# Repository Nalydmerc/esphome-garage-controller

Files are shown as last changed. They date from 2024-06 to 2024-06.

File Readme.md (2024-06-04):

### ESPHome Garage Door Controller

I am a forgetful man. I forget to close the garage door. My wife gets frustrated that I forget to close the garage door. I may or may not get slightly banned from the garage due to leaving the garage door open too many times after leaving for work. So, I do what any sensible man would do. I offload my responsibilities to technology, of course.

The device uses an ESP8266 running ESPHome to connect to HomeAssistant and do garage door things. I used a hall effect sensor to detect if each door was open or closed, but you could use any contact that opens/closes depending on the state of the door. To open and close the doors, I just wired in a relay in parallel with each button. YMMV, but for mine this did mean I had to physically disassemble each button and solder extra wires onto the PCB.

This project was designed to be cheap, as opposed to involved. You can build your own buck converters into your projects (I have in the past), but at the end of the day it's still cheaper to buy one of those cheap adjustable converters on aliexpress and call it a day. Sure there's 0.4V of switching noise, but the D1 Mini has a built in LDO anyway, as do most cheap development boards. ¯\\\_(ツ)\_/¯ A good project is one that is finished to spec, and my spec is that it works.

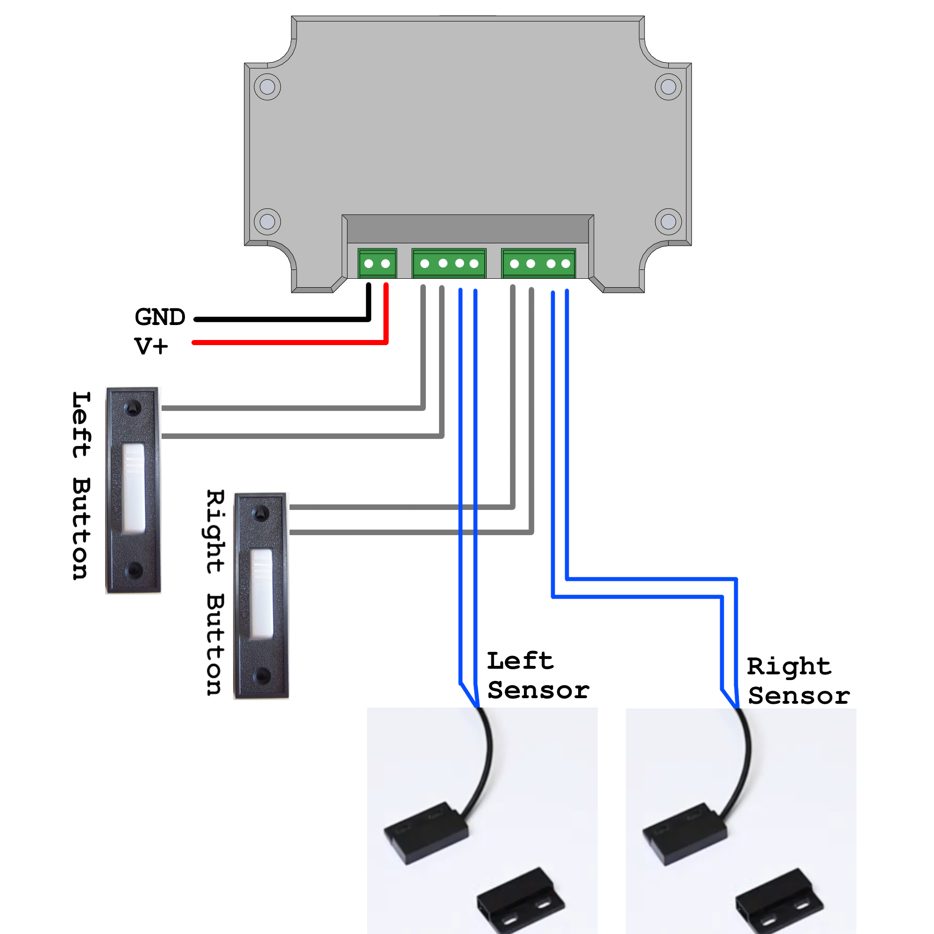
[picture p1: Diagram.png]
diagram


### Mechanical Assembly and Bill of Materials

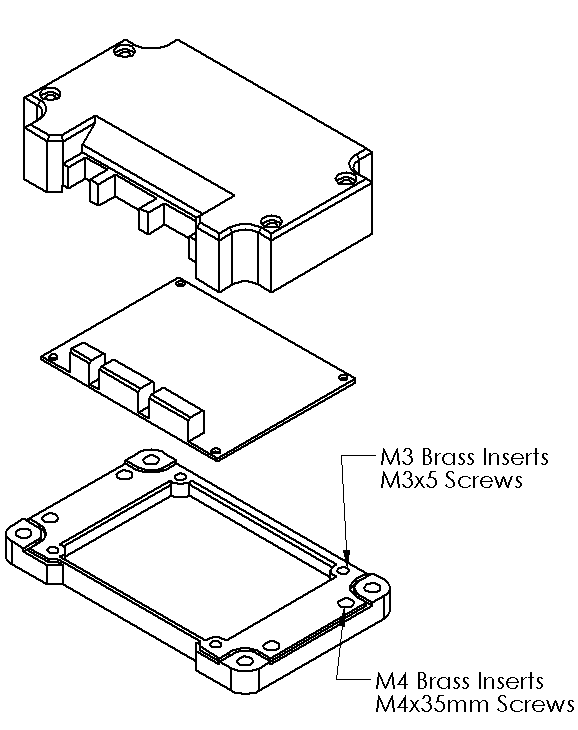
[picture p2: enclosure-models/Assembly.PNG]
mechanical assembly


.step files for a 3D printed enclosure are included in this project. The backplate uses M3 screws to mount the PCB, and M4 screws to attach the top. Other Non-PCB materials are as follows:

|Item | Qty|Link |
|--|--|--|
| Hall effect sensor |2| https://www.aliexpress.us/item/3256805925218267.html |
| Cabling || https://www.aliexpress.us/item/3256806428440404.html |
|Wire Ferrules (for crimping ends) || https://www.aliexpress.us/item/3256805075641713.html |
| Lever-nut connectors (love these) || https://www.aliexpress.us/item/3256803684080411.html |
| M3 Brass Inserts | 4 | https://www.aliexpress.us/item/3256803396040989.html |
| M3x5mm |4||
| M4 Brass Inserts | 4 | https://www.aliexpress.us/item/3256803396040989.html |
| M4x35mm |4||

### Manufacturing the PCB

If you want to make this PCB yourself, simply zip up the outputs folder and upload it to the PCB manufacturer of your choice. You can take the bill of materials CSV and upload it directly to digikey to create a cart with the needed components. Anything that doesn't have a digikey part number, I listed the relevant aliexpress product page.

### Random notes for myself

Reminder: Set switches to pins 5 and 4 to prevent them from toggling during startup. (esp8266s are weird. Never before have I had to deal with GPIOs just doing random things during the startup process.)

https://community.home-assistant.io/t/esp8266-relay-active-low-how-to-prevent-triggering-on-boot-or-reset-solved/88279/30
https://rabbithole.wwwdotorg.org/2017/03/28/esp8266-gpio.html

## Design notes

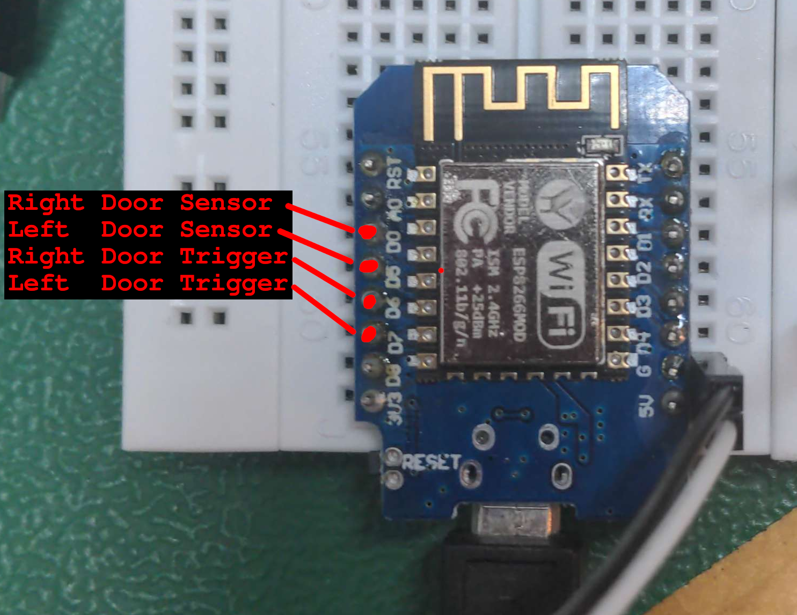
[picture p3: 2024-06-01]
prototype/Pinout.png

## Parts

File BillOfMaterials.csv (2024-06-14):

Reference | Value | Footprint | Qty | DNP | Digikey PN | PN
D1,D2 | 1N4148TR | Diode_THT:D_DO-35_SOD27_P10.16mm_Horizontal | 2 |  | 1N4148FSCT-ND | DIO-004
D3 | SMAJ12A | Diode_SMD:D_SMA_Handsoldering | 1 |  | SMAJ12ALFCT-ND | DIO-014
D4,D5 | SMA6J5.0A-TR | Diode_SMD:D_SMA_Handsoldering | 2 |  | 497-5938-1-ND | DIO-011
H1,H2,H3,H4 | MountingHole | MountingHole:MountingHole_3.2mm_M3 | 4
J1 | 1935161.0 | TerminalBlock:TerminalBlock_bornier-2_P5.08mm | 1 |  | https://www.aliexpress.us/item/3256805408760426.html | CON-005
J2,J3 | EB21A-04-C | TerminalBlock:TerminalBlock_bornier-4_P5.08mm | 2 |  | https://www.aliexpress.us/item/3256805408760426.html
JP1 | Jumper_2_Bridged | Connector_PinHeader_2.54mm:PinHeader_1x02_P2.54mm_Vertical | 1 |  | S9337-ND
K1,K2 | SRD-12VDC-SL-C | 000-Footprints:Relay_SPDT_Songle | 2 |  | https://www.aliexpress.us/item/3256802839040760.html
Q1,Q2 | BS170-D26Z | Package_TO_SOT_THT:TO-92_Inline_Wide | 2 |  | BS170-D26ZCT-ND | FET-002
Q3 | IRFR9024NTRLPBF | Package_TO_SOT_SMD:TO-252-2 | 1 |  | IRFR9024NTRLPBFCT-ND | FET-007
R1,R2,R3,R4 | 100k | Resistor_THT:R_Axial_DIN0207_L6.3mm_D2.5mm_P15.24mm_Horizontal | 4
S1 | EG1224 | 000-Footprints:SW_E-Switch_EG1224_SPDT_Angled | 1 |  | EG2585-ND | MISC-006
TP1,TP2,TP3,TP4,TP5 | TestPoint | TestPoint:TestPoint_Pad_1.5x1.5mm | 5
U1 | LM2596 | 000-Footprints:LM2596Module | 1 |  | https://www.aliexpress.us/item/3256804718557368.html | MISC-009
U2 | WeMos_D1_mini | 000-Footprints:wemos-d1-mini-with-pin-header-and-connector | 1 |  | https://www.aliexpress.us/item/3256805831695231.html

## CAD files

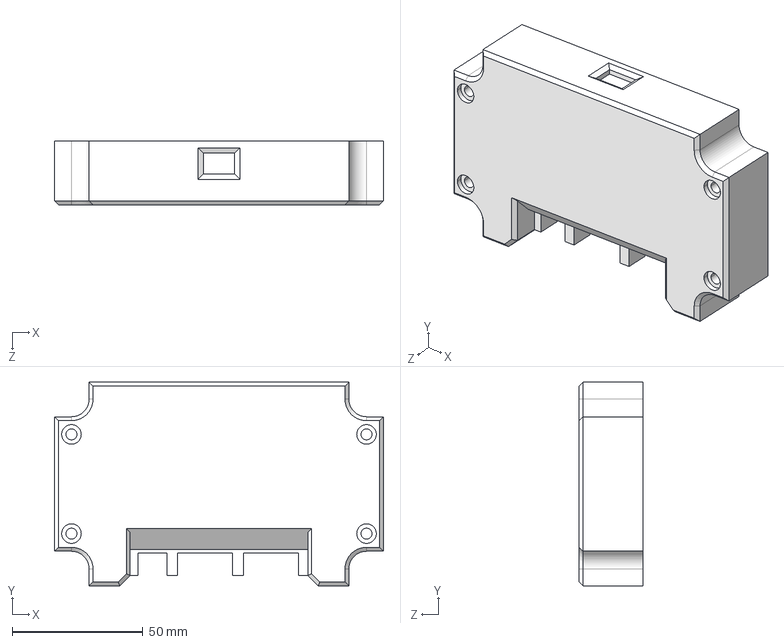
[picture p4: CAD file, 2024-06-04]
enclosure-models/Top.STEP
126.0 x 78.0 x 24.4 mm

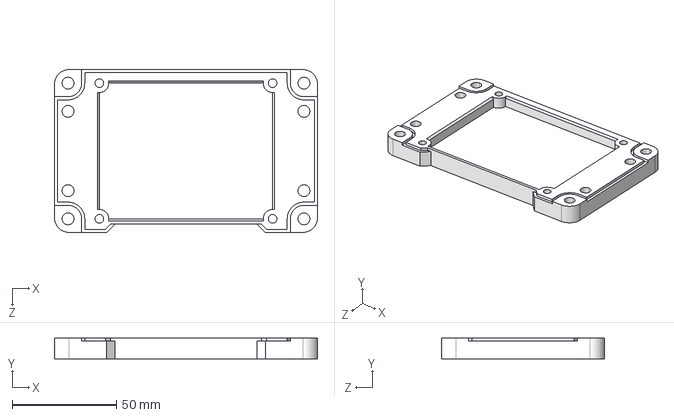
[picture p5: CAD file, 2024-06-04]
enclosure-models/Baseplate.STEP
126.0 x 10.0 x 78.0 mm

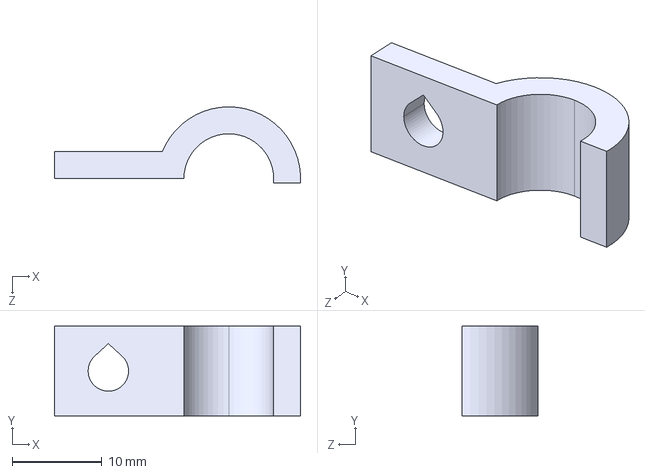
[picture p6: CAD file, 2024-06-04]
enclosure-models/Wireclip.STEP
27.4 x 10.0 x 8.50 mm

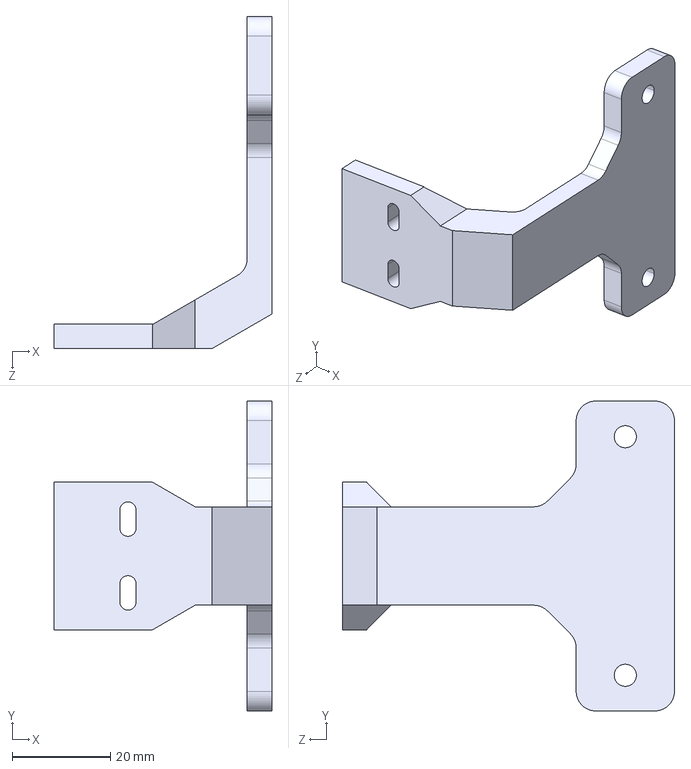
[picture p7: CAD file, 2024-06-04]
enclosure-models/SensorBracket.STEP
44.2 x 63.0 x 67.5 mm

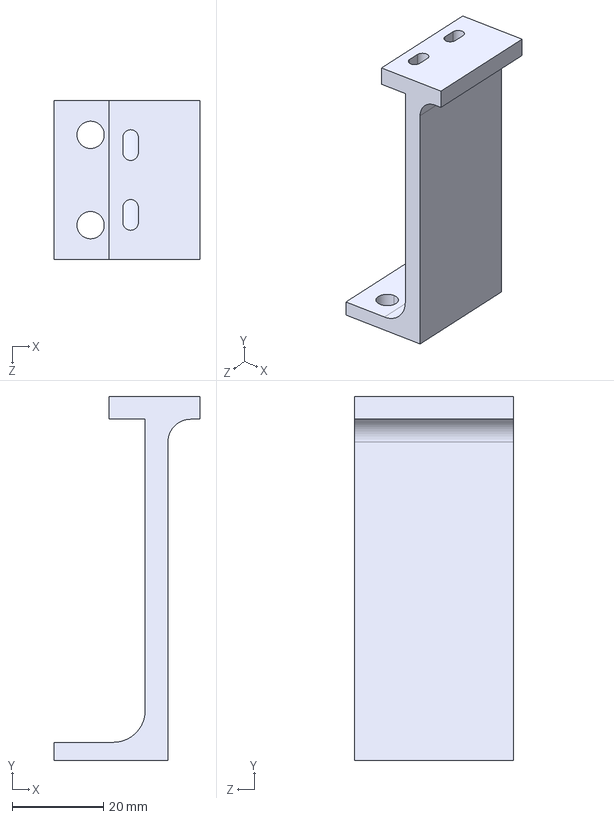
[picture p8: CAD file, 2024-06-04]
enclosure-models/MagnetBracket.STEP
32.0 x 80.0 x 35.0 mm

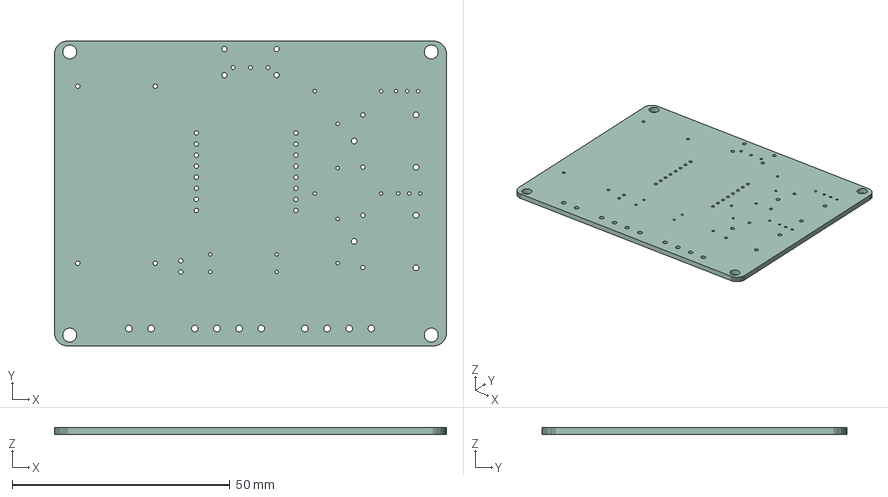
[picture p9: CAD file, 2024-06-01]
enclosure-models/pcb.step
90.0 x 70.0 x 1.60 mm

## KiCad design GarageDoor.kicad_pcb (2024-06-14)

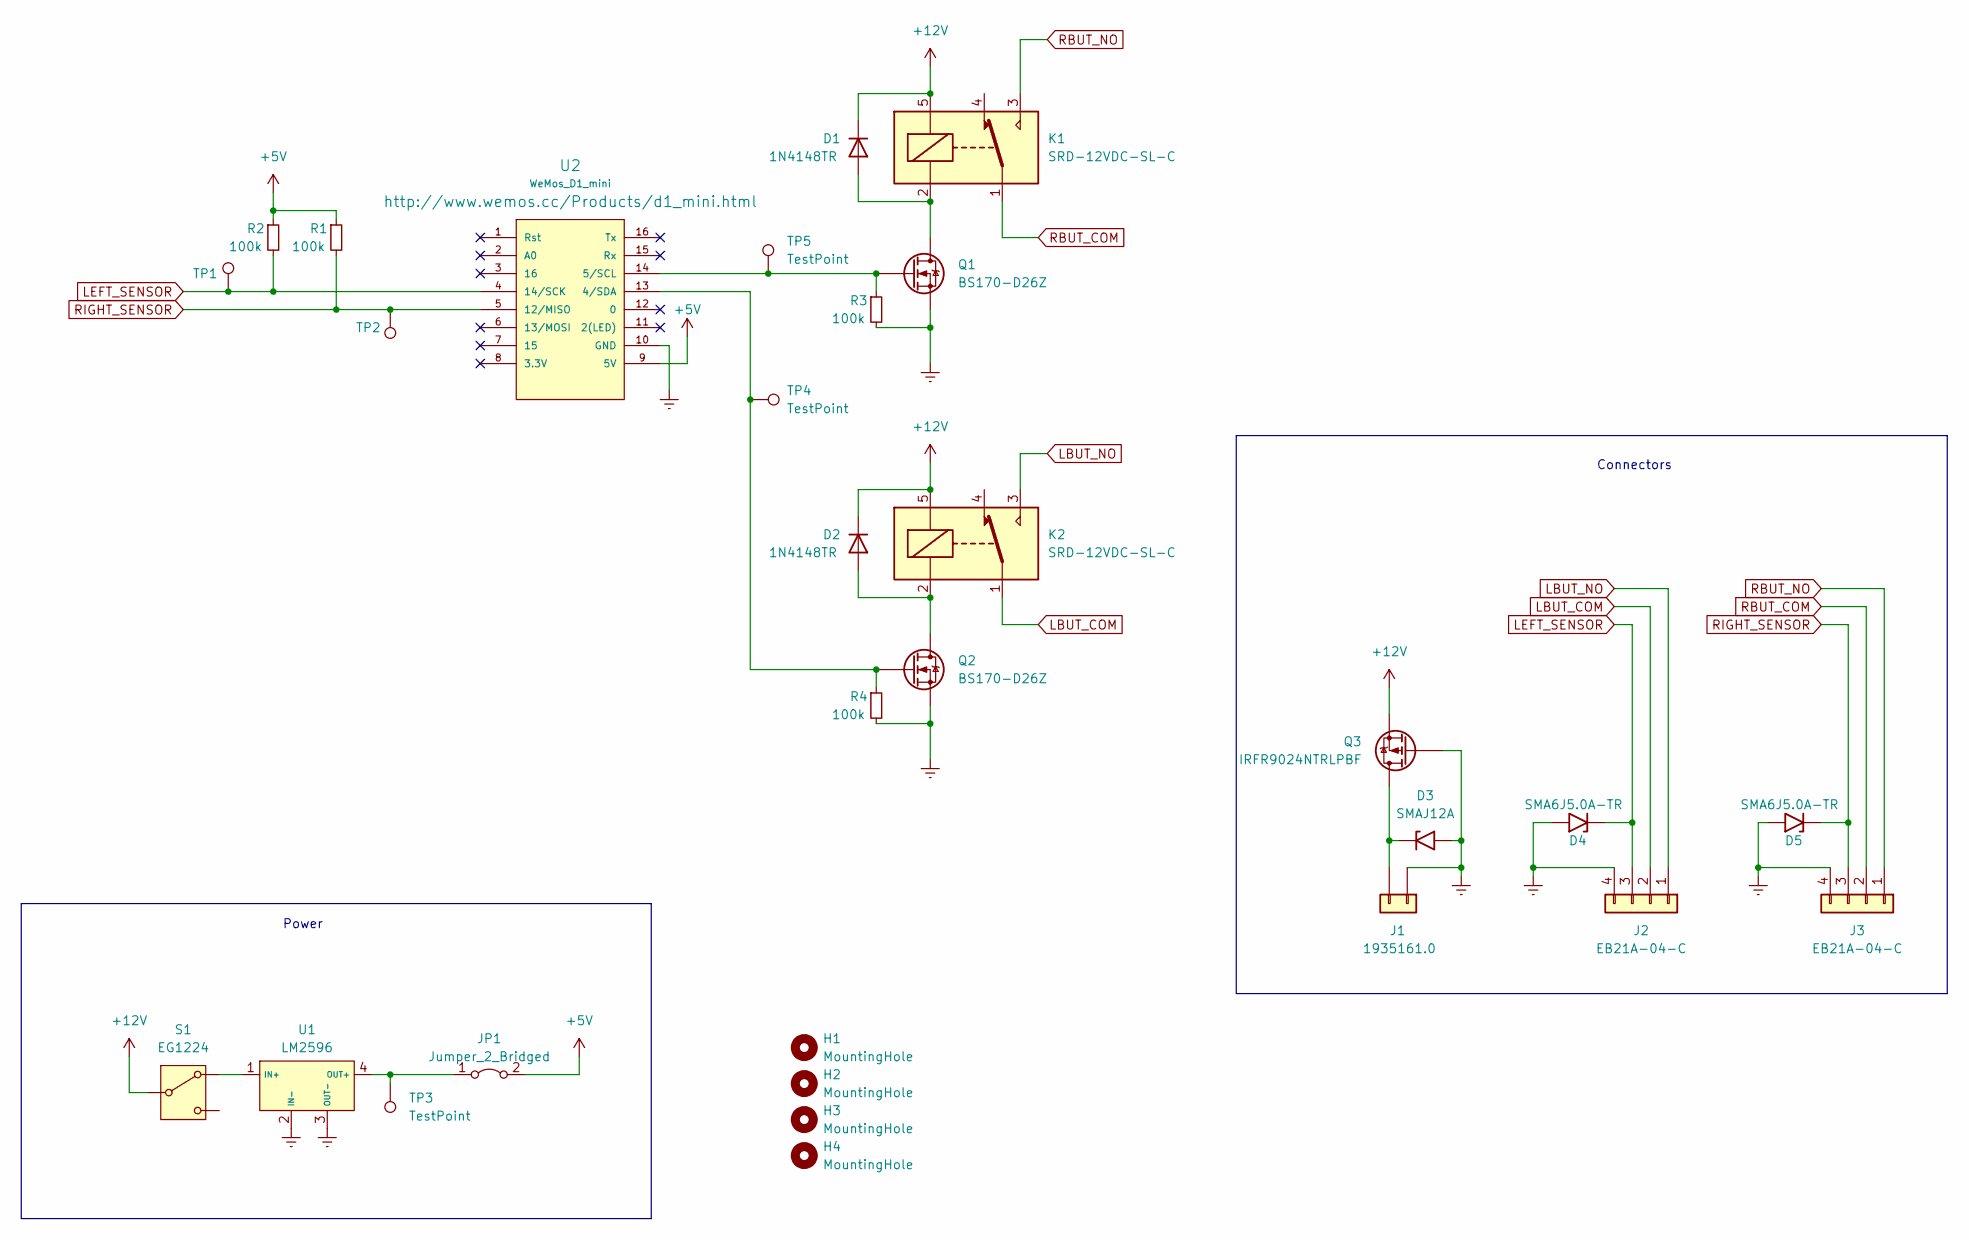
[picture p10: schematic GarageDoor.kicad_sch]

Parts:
D1, D2: 1N4148TR; D_DO-35_SOD27_P10.16mm_Horizontal; Digikey PN 1N4148FSCT-ND
D3: SMAJ12A; D_SMA_Handsoldering; Digikey PN SMAJ12ALFCT-ND
D4, D5: SMA6J5.0A-TR; D_SMA_Handsoldering; Digikey PN 497-5938-1-ND
H1, H2, H3, H4: MountingHole; MountingHole_3.2mm_M3
J1: 1935161.0; TerminalBlock_bornier-2_P5.08mm
J2, J3: EB21A-04-C; TerminalBlock_bornier-4_P5.08mm
JP1: Jumper_2_Bridged; PinHeader_1x02_P2.54mm_Vertical; Digikey PN S9337-ND
K1, K2: SRD-12VDC-SL-C; Relay_SPDT_Songle
Q1, Q2: BS170-D26Z; TO-92_Inline_Wide; Digikey PN BS170-D26ZCT-ND
Q3: IRFR9024NTRLPBF; TO-252-2; Digikey PN IRFR9024NTRLPBFCT-ND
R1, R2, R3, R4: 100k; R_Axial_DIN0207_L6.3mm_D2.5mm_P15.24mm_Horizontal
S1: EG1224; SW_E-Switch_EG1224_SPDT_Angled; Digikey PN EG2585-ND
TP1, TP2, TP3, TP4, TP5: TestPoint; TestPoint_Pad_1.5x1.5mm
U1: LM2596; LM2596Module
U2: WeMos_D1_mini; wemos-d1-mini-with-pin-header-and-connector

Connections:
+5V: JP1.2 (B), R1.1, R2.1, U2.9 (5V)
+12V: D1.1 (K), D2.1 (K), K1.5, K2.5, Q3.3 (S), S1.2 (B)
Earth: D3.2 (A2), D4.2 (A2), D5.2 (A2), J1.1, J2.4, J3.4, Q1.3 (S), Q2.3 (S), Q3.1 (G), R3.2, R4.2, U1.2 (IN-), U1.3 (OUT-), U2.10 (GND)
LBUT_COM: J2.2, K2.1
LBUT_NO: J2.1, K2.3
LEFT_SENSOR: D4.1 (A1), J2.3, R2.2, TP1.1, U2.4 (14/SCK)
unnamed: D1.2 (A), K1.2, Q1.1 (D)
unnamed: D2.2 (A), K2.2, Q2.1 (D)
unnamed: D3.1 (A1), J1.2, Q3.2 (D)
unnamed: JP1.1 (A), TP3.1, U1.4 (OUT+)
unnamed: Q1.2 (G), R3.1, TP5.1, U2.14 (5/SCL)
unnamed: Q2.2 (G), R4.1, TP4.1, U2.13 (4/SDA)
unnamed: S1.3 (A), U1.1 (IN+)
RBUT_COM: J3.2, K1.1
RBUT_NO: J3.1, K1.3
RIGHT_SENSOR: D5.1 (A1), J3.3, R1.2, TP2.1, U2.5 (12/MISO)

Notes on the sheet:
Connectors
Power

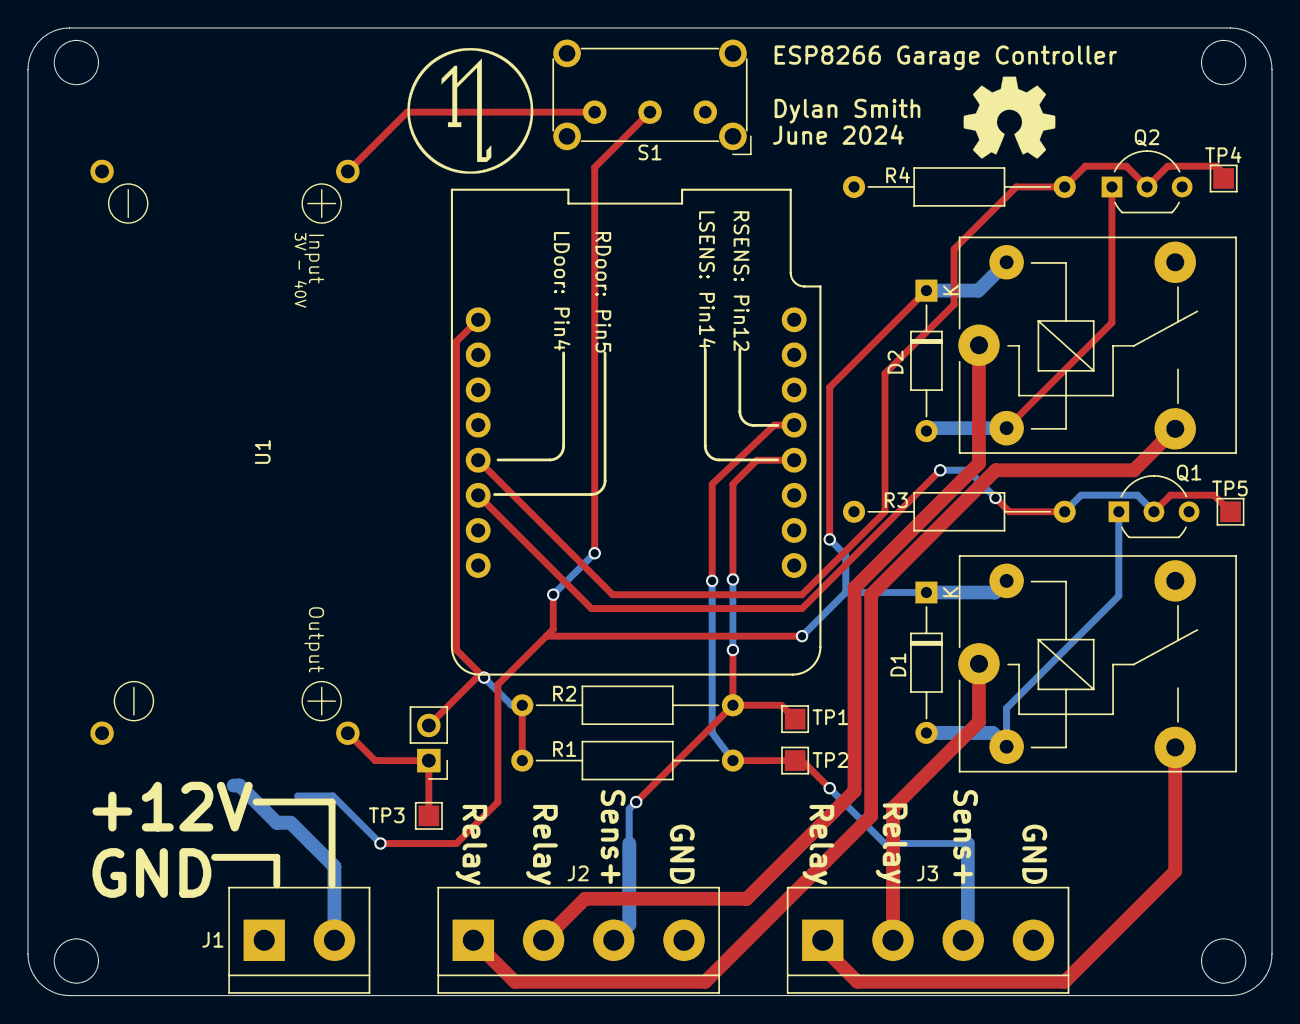
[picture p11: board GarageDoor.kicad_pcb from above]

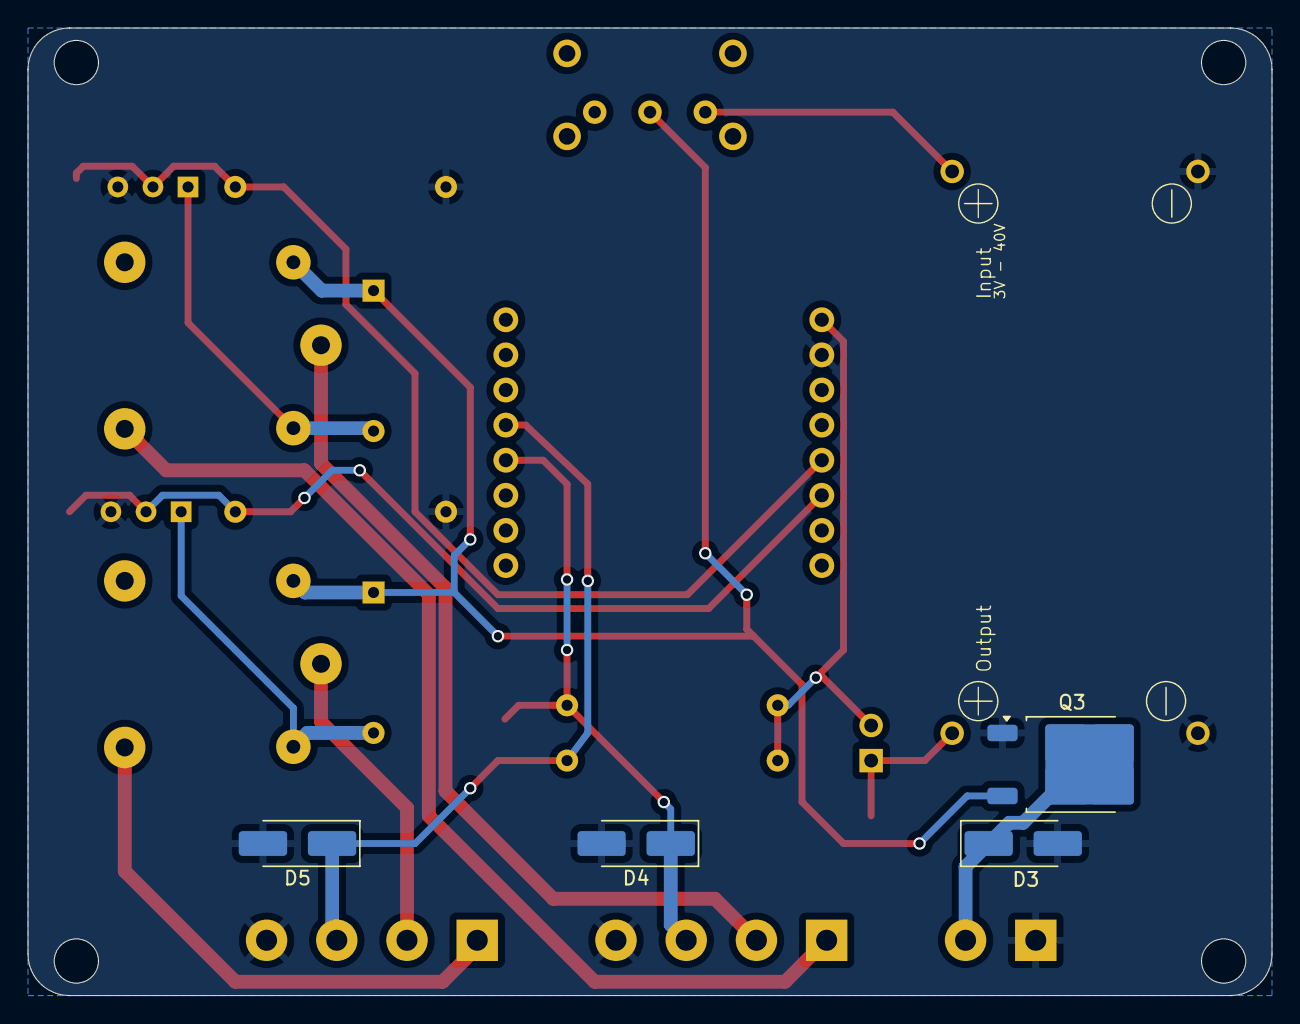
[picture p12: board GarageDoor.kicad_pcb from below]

Board: 2 copper layers, 90.0 x 70.0 mm, 30 parts (4 on the bottom side), 16 nets.

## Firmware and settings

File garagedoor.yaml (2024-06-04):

esphome:
  name: garagedoorsensor
  friendly_name: GarageDoorSensor

esp8266:
  board: d1_mini
  early_pin_init: false

# Enable logging
logger:

# Enable Home Assistant API
api:
  encryption:
    key: "YOUR_KEY_HERE"

ota:
  password: "ANOTHER_PASSWORD_HERE"

wifi:
  fast_connect: on
  ssid: !secret wifi_ssid
  password: !secret wifi_password
  use_address: YOUR_IP_HERE
  on_connect:
    - then:
      # Because of the circuit on the esp8266, switch.turn_on actually turns the LED OFF.
      # So look for the LED to turn OFF once it has successfully connected to wifi. 
      - switch.turn_on: led

  # Enable fallback hotspot (captive portal) in case wifi connection fails
  ap:
    ssid: "Garagedoorsensor"
    password: "YOUR_PASSWORD_HERE"

captive_portal:

binary_sensor:
  - platform: gpio
    pin: 12
    name: "Right Garage Door"
    device_class: garage_door
  - platform: gpio
    pin: 14
    name: "Left Garage Door"
    device_class: garage_door

switch:
  - platform: gpio
    pin: 5
    id: right_garage
    restore_mode: ALWAYS_OFF
  - platform: gpio
    pin: 4
    id: left_garage
    restore_mode: ALWAYS_OFF
  - platform: gpio
    pin: 2
    id: led


button:
  - platform: template
    name: Left Garage Button
    on_press:
      - then:
        - logger.log: "Left garage door toggled"
        - switch.turn_on: left_garage
        - delay: 500ms
        - switch.turn_off: left_garage
  - platform: template
    name: Right Garage Button
    on_press:
      - then:
        - logger.log: "Right garage door toggled"
        - switch.turn_on: right_garage
        - delay: 500ms
        - switch.turn_off: right_garage

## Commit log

2024-06-01 Initial commit.
    [GarageDoor-B_Cu.gbr, GarageDoor-B_Mask.gbr, GarageDoor-B_Paste.gbr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]
2024-06-02 Connect unused pins to ground.
    [GarageDoor.kicad_pcb, GarageDoor.kicad_sch]
2024-06-02 Move right sensor to pin 12 instead of 16, because that breaks everything for some reason and you're apparently just supposed to know that.
    [GarageDoor-B_Cu.gbr, GarageDoor-B_Mask.gbr, GarageDoor-B_Paste.gbr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]
2024-06-04 Add documentation.
    [Baseplate.STEP, BillOfMaterials.csv, GarageDoor.kicad_sch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]
2024-06-04 Added note about esp8266 LED
2024-06-04 Minor silkscreen change
    [GarageDoor-B_Cu.gbr, GarageDoor-B_Mask.gbr, GarageDoor-B_Paste.gbr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]
2024-06-14 Correct silkscreen. Update to Kicad 8.
    [BillOfMaterials.csv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]
